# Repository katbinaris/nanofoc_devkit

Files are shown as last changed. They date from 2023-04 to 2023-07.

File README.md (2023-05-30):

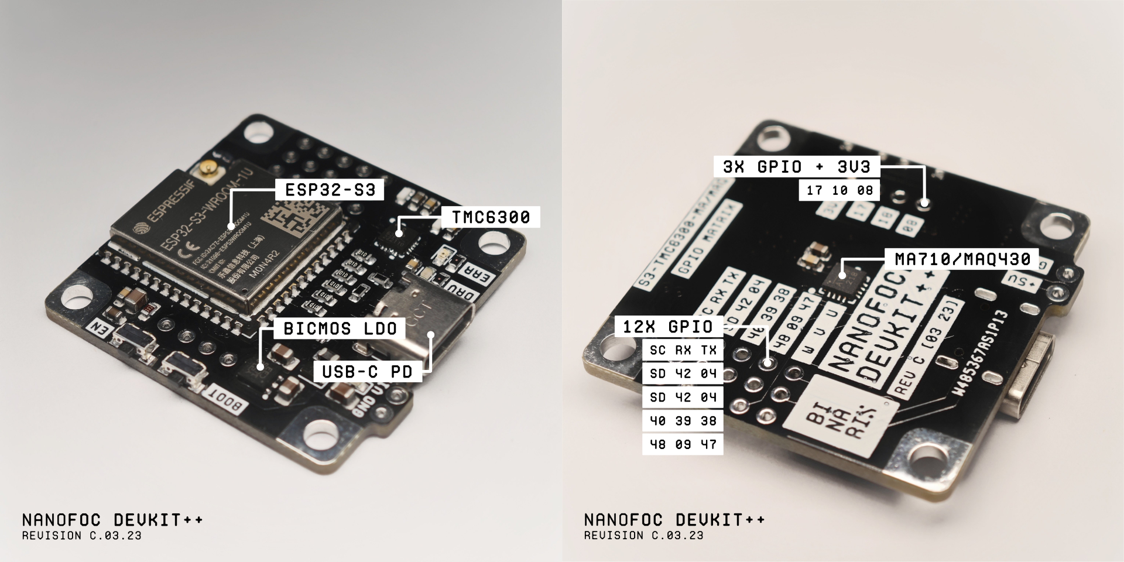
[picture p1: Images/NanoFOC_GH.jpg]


#### Product Description:
Starting your first Field Oriented Control (FOC) project might be daunting, especially if you're new to the field.

As makers, we frequently want to jump right into the action and begin writing the firmware without the hassle/need of selecting the right Microcontroller, Magnetic Sensor, and Motor Driver, then configuring and calibrating it with an abundance of cables that renders your projects too bulky to use in your creations.

The NanoFOC is little enough to attach on the back of most small BLDC gimbal motors (Even easier with Universal BLDC Motor Adapter Kit), making it an excellent choice for compact projects requiring maximum efficiency and precision.

Purchase Link: https://store.binaris.io/products/nanofoc-devkit

### Features:
- Espressif ESP32 S3 Microcontroller 4MB Flash, 2MB PSRAM 
- Trinamic TMC6300 low power 6PWM BLDC Driver
- MPS MagAlpha MA710 or MAQ430 rotary magnetic position sensor
- BiCMOS 3.3V LDO
- 11 Programmable GPIO's (SPI, PWM, ADC, RTC etc.)
- I2C & UART pins available
- USB Powered (Compatible with USB PD 2.0 - 5V @ 3A)
- USB OTG
- AUX Power via VIN pads 

### Pinout Cheat Sheet:
|  Pin | Function  | On GPIO Matrix? |
| --- | --- | --- |
| GPIO 01 | I2C SCL | YES |
| GPIO 02 |  I2C SDA | YES |
| GPIO 04 |  SPI CS -MAGNETIC SESNOR | NO |
| GPIO 05 |  SPI MOSI -MAGNETIC SESNOR | NO |
| GPIO 06 |  SPI SCLK -MAGNETIC SESNOR | NO |
| GPIO 07 |  SPI MISO -MAGNETIC SESNOR | NO |
| GPIO 08 |  I/O  | YES |
| GPIO 09 |  I/O  | YES |
| GPIO 10 |  VL - PhaseB Low  | NO |
| GPIO 11 |  WL - PhaseC Low  | NO |
| GPIO 12 |  UL - PhaseA Low  | NO |
| GPIO 13 |  WH - PhaseC High  | NO |
| GPIO 14 |  VH - PhaseB High  | NO |
| GPIO 17 |  I/O  | YES |
| GPIO 18 |  I/O  | YES |
| GPIO 19 |  USB D- | NO |
| GPIO 20 |  USB D+ | NO |
| GPIO 21 |  UH PhaseA High | NO |
| GPIO 38 |  I/O  | YES |
| GPIO 39 |  I/O  | YES |
| GPIO 40 |  I/O  | YES |
| GPIO 41 |  I/O  | YES |
| GPIO 42 |  I/O  | YES |
| GPIO 43 | UART0 TX or I/O  | YES |
| GPIO 44 | UART0 RX or I/O | YES |
| GPIO 43 | UART0 TX  | YES |
| GPIO 44 | UART0 RX | YES |
| GPIO 47 | I/O | YES |
| GPIO 48 | I/O | YES |

### Board Layout:

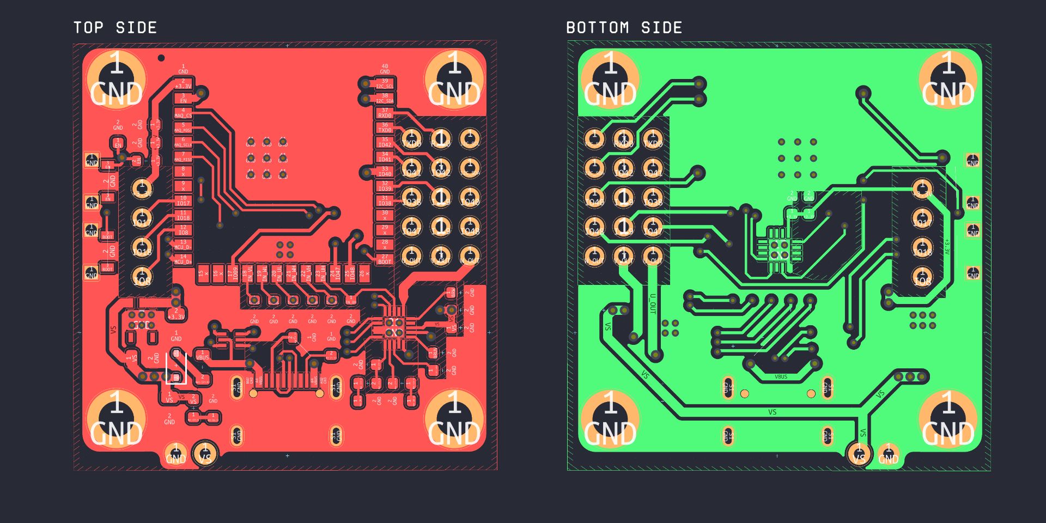
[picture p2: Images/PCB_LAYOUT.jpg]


### Bill Of Materials

| Component | References | Footprint | Quantity | Link | Price |
| --- | --- | --- | --- | --- | --- |
| 100nF | C1, C2, C4, C8, C12 | 0603 | 5 | https://eu.mouser.com/ProductDetail/KEMET/C0603C104K8RAC | 0,55 € |
| 4.7uF | C5, C6 | 0805 | 2 | https://eu.mouser.com/ProductDetail/TDK/C2012X7R1A475K125AC | 0,46 € |
| 10uF | C7, C13 | 0603 | 2 | https://eu.mouser.com/ProductDetail/Samsung-Electro-Mechanics/CL10A106KP8NNWC | 0,24 € |
| 22uf | C9 | 0805 | 1 | https://eu.mouser.com/ProductDetail/Murata-Electronics/GRM21BC81C226ME44L | 0,39 € |
| 22uf | C11 | 0603 | 1 | https://eu.mouser.com/ProductDetail/Murata-Electronics/GRM188R61A226ME15J | 0,17 € |
| 100K | R1-R6 | 0603 | 6 | https://eu.mouser.com/ProductDetail/Bourns/CMP0603-FX-1003ELF | 1,20 € |
| 300R | R7, R8 | 0603 | 2 | https://eu.mouser.com/ProductDetail/Panasonic/ERJ-UP3F3000V | 0,48 € |
| 150m | R9, R10 | 0603 | 2 | https://eu.mouser.com/ProductDetail/Susumu/KRL0816D-C-R150-F-T5 | 1,20 € |
| 340R | R14 | 0603 | 1 | https://eu.mouser.com/ProductDetail/Panasonic/ERJ-3EKF3400V | 0,09 €|
| 5.1K | R13 | 0603 | 2 | https://eu.mouser.com/ProductDetail/Panasonic/ERJ-P03F5101V | 0,70 € |
| 10K | R15 | 0603 | 1 | https://eu.mouser.com/ProductDetail/ROHM-Semiconductor/SFR03EZPF1002 | 0,13 € |
| 100Mhz 400Ohm 1.5A | L1 | 0805 |  1 | https://eu.mouser.com/ProductDetail/Laird-Performance-Materials/MI0805K400R-10 | 0,19 €  |
| NUF2042XV6T1G | D3 | SOT-563 | 1 | https://www.mouser.com/ProductDetail/onsemi/NUF2042XV6T1G | 0,44 € |
| CUS15S30 | D4 | SOD-323 | 1 | https://www.mouser.com/ProductDetail/Toshiba/CUS15S30H3F | 0,33 € |
| Yellow/Green Mono LED | D5, DRV | 0603 | 2 | https://eu.mouser.com/ProductDetail/ROHM-Semiconductor/SML-D12M8WT86 | 0,68 € |
| ESP32-S3 N4R2 1U | U1 | ESP32-S3-WROOM-1U | 1 | https://www.mouser.com/ProductDetail/Espressif-Systems/ESP32-S3-WROOM-1U-N8R2 | 3,38 € |
| TMC6300 LA | U2 | QFN20 | 1 | https://eu.mouser.com/ProductDetail/ADI-Trinamic/TMC6300-LA-T | 2,13 € |
| MPS MA710| U3 | QFN16 | 1 | https://www.mouser.com/ProductDetail/Monolithic-Power-Systems-MPS/MA710GQ-Z | 6,15 € |
| Alps SKTDLDE010 | SW1, SW2 | SKTDLDE010 | 2 | https://eu.mouser.com/ProductDetail/Alps-Alpine/SKTDLDE010 | 1,46 € |
| Amber Mono LED | ERR | 0603 | 1 | https://eu.mouser.com/ProductDetail/Wurth-Elektronik/150060AS75000 | 0,14 € |
| ST1L05CPU33R LDO | IC1 | DFN6 | 1 | https://www.mouser.com/ProductDetail/STMicroelectronics/ST1L05CPU33R | 1,18 € |
| G-Switch_GT-USB-7010ASV | P1 | 7010ASV | 1 | https://www.mouser.com/ProductDetail/GCT/USB4105-GF-A | 0,75 € | 
| | | | **38** | | **22,44 € / 23.50 $** |

### Power Options:
Device is designed to run of 5V @ 1.5A Max.
There are two ways you can power the board 

1. USB Type C - Power delivery is capped at 5V3A with usage of 5.1K resistors on CC1 and CC2 pads. It is recommended to use USB that is PD2.0 compatible.
It is possible to power device off 500mA capable USB port - however this is not recommended.

2. External VIN  - This connection bypass L1 and  D4 connecting directly to Driver and LDO VS pin. The recommended input voltage is 5V and maximum allowed is 6V - which is restricted by max VIN of ST1L05C LDO.

### First Time Setup
Development Kit comes with no Firmware.
Since ESP32-S3 comes with USB-OTG/USB-Serial integrated into MCU the assumption is that this would be a preferred method of code upload.
If you are connecting your device to computer for the first time it is critical to put device into DFU mode.

**In order to do that you need to:**
1. Connect Development Board to USB port - *On windows machines you may notice that USB detection sound goes on and off in loop - Please ignore that for now*
2. Press and hold **BOOT** switch
3. While holding **BOOT** press and hold **RESET** switch for about **2 seconds**
4. Release **RESET**
5. Release **BOOT**
6. You are now in **DFU mode** and you can use Arduino IDE or PlatformIO to upload your first sketch.

Alternatively you may use UART pins which are available on GPIO Matrix to upload your code the legacy way.
In order to do that you need external TTL Converter.

### Projects using NanoFOC:

SmartKnob by Scott Bezek -> https://github.com/scottbez1/smartknob#nanofoc-3rd-party

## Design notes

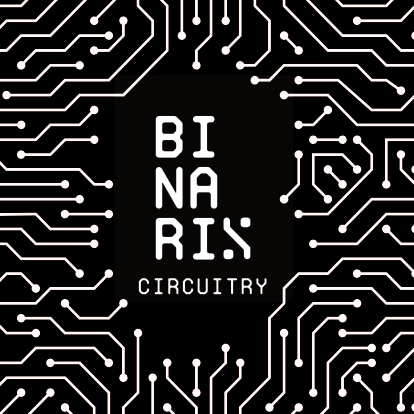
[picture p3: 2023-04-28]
Images/Sticker_large.png

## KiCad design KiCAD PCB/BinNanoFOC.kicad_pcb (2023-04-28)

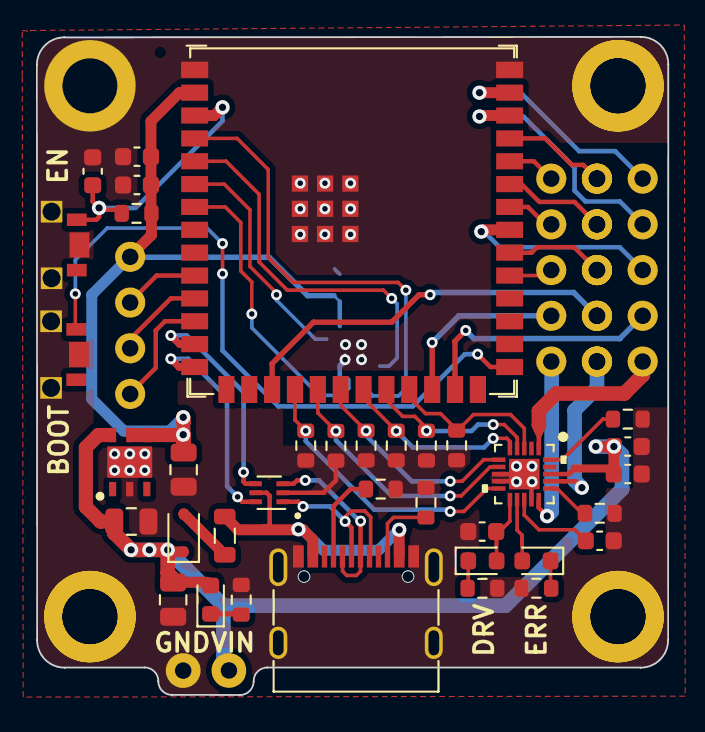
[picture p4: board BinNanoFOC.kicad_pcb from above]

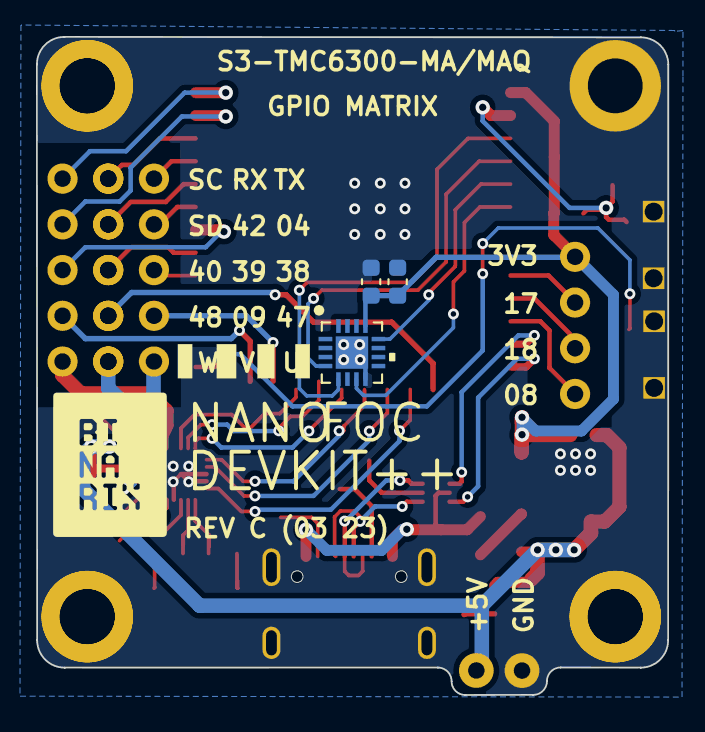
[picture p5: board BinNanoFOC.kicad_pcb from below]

Board: 2 copper layers, 35.1 x 36.6 mm, 39 parts (3 on the bottom side), 30 nets.

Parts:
C1, C2, C4, C8, C12: 100nF; C_0603_1608Metric
C3: 10uF; C_0603_1608Metric
C5, C6: 4.7uF; C_0805_2012Metric
C7, C13: 1uF; C_0603_1608Metric
C9: 22uF; C_0805_2012Metric
C11: 22uF; C_0603_1608Metric
D3: NUF2042XV6T1G; SOT-563
D4: D; D_SOD-323
D5: LED; LED_0603_1608Metric
DIAG: ERROR; LED_0603_1608Metric
DRV: DRIVER; LED_0603_1608Metric
IC1: ST1L05CPU33R; SON95P300X300X100-7N-D
L1: 100Mhz 40Ohm 1.5A; L_0805_2012Metric
P1: USB_C_Plug; USB_C_Receptacle_G-Switch_GT-USB-7010ASV
R1, R2, R3, R4, R5, R6: 100K; R_0603_1608Metric
R7, R8: 300R; R_0603_1608Metric
R9, R10: 300M; R_0603_1608Metric
R13, R13#2: 5.1K; R_0603_1608Metric
R14: 350R; R_0603_1608Metric
R15: 10K; R_0603_1608Metric
SW1, SW2: SW_MEC_5E; SKTDLDE010
U1: ESP32-S3-WROOM-1; ESP32-S3-WROOM-1U
U2: TMC6300-LA
U3: MAQ430GQE-AEC1-P

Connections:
+3.3V: C6.2, C7.1, C8.1, C11.1, C12.1, IC1.4 (VO), IC1.5 (V_O_SENSE), R15.1, U1.2 (3V3), U3.13 (VDD)
BOOT: SW1.3 (K), U1.27 (GPIO0/BOOT)
BRUV: R9.1, U2.16 (BRUV)
BRW: R10.1, U2.20 (BRW)
EN: C13.1, R15.2, SW2.3 (K), U1.3 (EN)
GND: C1.2, C2.2, C3.2, C4.2, C5.2, C6.1, C7.2, C8.2, C9.2, C11.2, C12.2, C13.2, D3.2 (GND), IC1.2 (GND), IC1.7 (EP), P1.A1 (GND), P1.A12 (GND), P1.B1 (GND), P1.B12 (GND), P1.S1 (SHIELD), R1.2, R2.2, R3.2, R4.2, R5.2, R6.2, R7.2, R8.2, R9.2, R10.2, R13.1, R13#2.1, R14.2, SW1.1, SW1.2, SW2.1, SW2.2, U1.1 (GND), U1.40 (GND), U1.41 (GND), U2.8 (GND), U2.9 (GND), U2.14 (GND), U2.21 (EPAD), U3.8 (GND), U3.17 (PAD)
IN_UH: R6.1, U1.23 (GPIO21), U2.3 (UH)
IN_UL: R3.1, U1.20 (GPIO12/TOUCH12/ADC2_CH1/FSPICLK/FSPIIO6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), U2.6 (UL)
IN_VH: R5.1, U1.22 (GPIO14/TOUCH14/ADC2_CH3/FSPIWP/FSPIDQS/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), U2.4 (VH)
IN_VL: R1.1, U1.18 (GPIO10/TOUCH10/ADC1_CH9/FSPICS0/FSPIIO4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), U2.10 (VL)
IN_WH: R4.1, U1.21 (GPIO13/TOUCH13/ADC2_CH2/FSPIQ/FSPIIO7/S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), U2.5 (WH)
IN_WL: R2.1, U1.19 (GPIO11/TOUCH11/ADC2_CH0/FSPID/FSPIIO5/S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), U2.7 (WL)
MAQ_CS: U1.4 (GPIO4/TOUCH4/ADC1_CH3), U3.5 (CS)
MAQ_MISO: U1.7 (GPIO7/TOUCH7/ADC1_CH6), U3.7 (MISO)
MAQ_MOSI: U1.5 (GPIO5/TOUCH5/ADC1_CH4), U3.4 (MOSI)
MAQ_SCLK: U1.6 (GPIO6/TOUCH6/ADC1_CH5), U3.12 (SCLK)
MCU_D+: D3.6 (D1(0)), U1.14 (GPIO20/U1CTS/ADC2_CH9/CLK_OUT1/USB_D+)
MCU_D-: D3.4 (D2(0)), U1.13 (GPIO19/U1RTS/ADC2_CH8/CLK_OUT2/USB_D-)
unnamed: C1.1, DRV.2 (A), U2.11 (VIO/NSTDBY)
unnamed: DRV.1 (K), R7.1
unnamed: DIAG.2 (A), U2.12 (DIAG)
unnamed: DIAG.1 (K), R8.1
unnamed: D4.2 (A), L1.2
unnamed: D5.1 (K), R14.1
unnamed: P1.A5 (CC), P1.B5 (VCONN), R13.2, R13#2.2
unnamed: C2.1, U2.13 (1-8VOUT)
USB_D+: D3.1 (D1(I)), P1.A6 (D+), P1.B6
USB_D-: D3.3 (D2(I)), P1.A7 (D-), P1.B7
VBUS: D3.5 (VBUS), L1.1, P1.A4 (VBUS), P1.A9 (VBUS), P1.B4 (VBUS), P1.B9 (VBUS)
VS: C3.1, C4.1, C5.1, C9.1, D4.1 (K), D5.2 (A), IC1.6 (VI), U2.18 (VS)

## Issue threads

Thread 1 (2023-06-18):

BOM mistake

giklette, 2023-06-18:
on the README.md
goto the BOM components : https://github.com/katbinaris/nanofoc_devkit#bill-of-materials

should replace the row C7, C13 by C7, C3
and add new row
> 1uf      |    C13     |     0603    |      1     |     // mouser reference //

- C3 is 10uF
- C13 is 1uF    not   10uF

Jogius, 2024-03-22:
C7 is also 1uF, according to the PCB file. So C7 and C13 should be 1uF instead of 10uF, and C3 needs to be added to the file altogether.

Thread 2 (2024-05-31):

Schematic for LDO incorrect / wrong part number (ST1L05CPU33R)

Jogius, 2024-05-31:
I tried assembling my first nanofoc yesterday and I think I might've found a small mistake in the schematic or in the part listed.

The LDO is an ST1L05CPU33R, which is listed under ST1L05C in the datasheets. This version of the LDO has an enable Pin, which is not connected on the PCB. I was able to make a small bridge to the capacitor right next to it, which successfully enabled the 3.3V output.
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

I believe the part should either be an ST1L05 (without the C) or there needs to be another connection to this chip.

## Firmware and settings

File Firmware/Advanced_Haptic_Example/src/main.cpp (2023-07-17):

#include <Arduino.h> // PIO Specific Call Arduino Core
#include <SimpleFOC.h> // Call FOC Library
#include <utils.h> // ESP32 Specific utility that clamps a middle value witin a range of values between a defined min and max bound.

// Driver Logic Pin Defs
#define PIN_UH 21
#define PIN_UL 12
#define PIN_VH 14
#define PIN_VL 10
#define PIN_WH 13
#define PIN_WL 11
// Sensor nCS pin
#define MAQ_SS 4
//Motor Pole Pair Count
#define MOTOR_PP 7 

// Static construct set for Dead Zone Compensation and EWMA correction.
static const float DEAD_ZONE_DETENT_PERCENT = 0.2;
static const float DEAD_ZONE_RAD = 1 * _PI / 180;
static const float IDLE_VELOCITY_EWMA_ALPHA = 0.001;
static const float IDLE_VELOCITY_RAD_PER_SEC = 0.05;
static const uint32_t IDLE_CORRECTION_DELAY_MILLIS = 500;
static const float IDLE_CORRECTION_MAX_ANGLE_RAD = 5 * PI / 180;
static const float IDLE_CORRECTION_RATE_ALPHA = 0.0005;

// Default Haptic Program Variables
int32_t position = 0;
int32_t num_positions = 360;
float position_with_radians = 2.5*_PI/180.0;;
float haptic_strength_unit = 0.2;
float haptic_endstop_strength_unit = 1.4;
float haptic_dampening_factor = 5500; // min 50 max 7500
float snap_point = 0.545;
float sub_position_unit;

 
  float idle_check_velocity_ewma = 0;
  uint32_t last_idle_start = 0;
  uint32_t last_publish = 0;

  const float derivative_lower_strength = haptic_strength_unit * 0.148;
  const float derivative_upper_strength = haptic_strength_unit * 0.008;
  const float derivative_position_width_lower = radians(3); // 3 Degrees represented in radians
  const float derivative_position_width_upper = radians(8); // 8 Dergees represented in radians
  const float raw = derivative_lower_strength + (derivative_upper_strength - derivative_lower_strength)/(derivative_position_width_upper - derivative_position_width_lower)*(position_with_radians - derivative_position_width_lower);



// This code is optimized to works well with MAD2804 motor.

// Call a MagneticSensoSPI driver in SimpleFOC libdep.
// You will need to manually add definiton of the sensor to MagneticSensorSPI.h and MagneticSensorSPI.cpp
// .pio/libdeps/adafruit_feather_esp32s3/SimpleFOC/src/drivers/sensors
// Correct version of the file for SimpleFOC 2.3 can be found in GitHub repository
MagneticSensorSPI sensor = MagneticSensorSPI(MAQ430_SPI, MAQ_SS); 

// Define number of Stator Pole Pairs - Usually this number resides between 7-11 for most gimbal motors
// If you're unsure how many pole pairs your motor has, SimpleFOC calibration would help you estimating PP Count
// Alternatively SimpleFOC has example code "Pole Pair Estimator"
BLDCMotor motor = BLDCMotor(MOTOR_PP);
// BLDCDriver6PWM(PIN_UH, PIN_UL, PIN_VH, PIN_VL, PIN_WH, PIN_WL);
BLDCDriver6PWM driver = BLDCDriver6PWM(PIN_UH, PIN_UL, PIN_VH, PIN_VL, PIN_WH, PIN_WL);

void setup() {

  // SimpleFOC Setup

  // initialise magnetic sensor hardware
  sensor.init();

  // link the motor to the sensor
  motor.linkSensor(&sensor);

  // Driver Configuration
  // power supply voltage [V]
  driver.voltage_power_supply = 5;

  // Driver Voltage limit - A way to limit PWM duty cycle
  // For NanoFOC DevKit this value is between 2-5V
  // Do not exceed 5V as you might damage the driver
  driver.voltage_limit = 3;

  // Driver PWM Frequency - Higher the value the smoother operation in theory.
  // If unsure leave commented, Values can range from 8000-50000 (Hz)
  // driver.pwm_frequency = 50000;

  // Initialize Driver
  driver.init();
  // Link the motor and the driver
  motor.linkDriver(&driver);

  // For Haptic Feedback we will be using Torque controller
  // Torque Controller can be controlled by Voltage (Default), Voltage - Estimated Current, DC Current and FOC Current modes.
  
  motor.controller = MotionControlType::torque;

  // If you know your motor phase resistance
  // You can uncomment this section, and you will be operating in "Voltage - Estimated Current" mode.
  // It is much more natural to control haptics with Current rather than Voltage
  // motor.phase_resistance = 4.4; // ex. 2.5 Ohms

  // If you know your motor KV rating (V/RPM) you may instert it here. KV is proportional to target voltage.
  // Most of manufacturers provide KV rating for rated Voltage, It is advised to perform your own KV rating.
  // You can do this by running SimpleFOC KV Rating example code.
  // Please add 10-20% overhead on top of your KV estimation
  //motor.KV_rating = 115;

  // IMPORTANT
  // By introducing Phase Resistance and KV Rating you would need drastically lower your PID values
  // If you decide to introuce Phase R and KV rating start from PID 0,0,0,250,5
  // High probability that BEMF/Inductance spike will damage VBUS diode and LDO if not used correctly


  // Very Basic PID Controller
  // haptic attraction controller - only Proportional + Derivative (Ignore Intergal == 0)
  // P = Proportional, responsible for reactiveness, Values between 0.1 - 1.5 are acceptable for most of motors.
  // D = Derivative, responsible for introducing resistance - similar to viscose friction. Use this to counteract cogging torque or in combination with Proportional. (Keep values low between 0.01 = 0.14)
  // Output_Ramp = Output Derivative limit [V/s] - depending on motor keep it between 100-2500. Non NdFeB drives can use higher values.
  // Limit = Output supply limit [V] - Keep at 3 or less unless you understand what you're doing.
  // [IMPORTANT] If you're not using MAD2804 motor start tuning from PID{0,0,0,100,1}
  // Set motor voltage limit (it is safe to keep it between 2.5-5V, depending on motor is recommended 3V)
  motor.voltage_limit = 3;   // [V]
  motor.PID_velocity.P = 1; // Proportional Gain is further calculated adaptively
  motor.PID_velocity.I = 0; // Intergal Gain remain at "0"
  motor.PID_velocity.D = 0.48; // Derivative Gain is further calculated adaptively as well
  motor.PID_velocity.output_ramp = haptic_dampening_factor; // TODO Output Ramp need to be adaptive 
  motor.PID_velocity.limit = 3; // Velocity limit is further calculated adaptively

  // Velocity Low Pass Filtering
  // Default value is 5ms - You an try different values to see what is best for your motor
  // The lower value the less filtering
  // motor.LPF_velocity.Tf = 0.015;// to set it to 10ms
  // As above but for angle (does not override velocity Low Pass Filtering)
  motor.LPF_angle.Tf = 0.0075;
  
  motor.PID_velocity.D = CLAMP(
    raw,
    min(derivative_lower_strength, derivative_upper_strength),
    max(derivative_lower_strength, derivative_upper_strength)
  );

  // Use monitoring with serial 
  Serial.begin(115200);

  // Comment out if not needed
  motor.useMonitoring(Serial);

  // Initialize motor
  motor.init();
  

  // Align sensor, PP check + Eletrical Zero, if pass start FOC
  motor.initFOC(4.6, Direction::CW);

  Serial.println("Haptic Device Ready :)");
  _delay(500);

  

}

float current_angle_center = -motor.shaft_angle;

void loop() {
 
  // Main FOC algorithm function
  motor.loopFOC();

 // If we are not moving and we're close to the center (but not exactly there), slowly adjust the centerpoint to match the current position
  idle_check_velocity_ewma = motor.shaft_velocity * IDLE_VELOCITY_EWMA_ALPHA + idle_check_velocity_ewma * (1 - IDLE_VELOCITY_EWMA_ALPHA);
  if (fabsf(idle_check_velocity_ewma) > IDLE_VELOCITY_RAD_PER_SEC) {
      last_idle_start = 0;
  } else {
      if (last_idle_start == 0) {
          last_idle_start = millis();
      }
  }
  if (last_idle_start > 0 && millis() - last_idle_start > IDLE_CORRECTION_DELAY_MILLIS && fabsf(motor.shaft_angle - current_angle_center) < IDLE_CORRECTION_MAX_ANGLE_RAD) {
      current_angle_center = motor.shaft_angle * IDLE_CORRECTION_RATE_ALPHA + current_angle_center * (1 - IDLE_CORRECTION_RATE_ALPHA);
  }

float position_to_indent_center = -motor.shaft_angle - current_angle_center;

if (position_to_indent_center > position_with_radians * snap_point && (num_positions <= 0 || position > 0)) {
            current_angle_center += position_with_radians;
            position_to_indent_center -= position_with_radians;
            position--;
            
        } else if (position_to_indent_center < -position_with_radians * snap_point && (num_positions <= 0 || position < num_positions - 1)) {
            current_angle_center -= position_with_radians;
            position_to_indent_center += position_with_radians;
            position++;
           
        }

float dead_zone_adjustment = CLAMP(
  position_to_indent_center,
  fmaxf(-position_with_radians*DEAD_ZONE_DETENT_PERCENT, -DEAD_ZONE_RAD),
  fminf(position_with_radians*DEAD_ZONE_DETENT_PERCENT, DEAD_ZONE_RAD));

bool out_of_range = num_positions > 0 && ((position_to_indent_center > 0 && position == 0) || (position_to_indent_center < 0 && position == num_positions - 1));
motor.PID_velocity.limit = 20;
motor.PID_velocity.P = out_of_range ? haptic_endstop_strength_unit : 3.4;

// Apply motor torque based on our angle to the nearest detent (detent strength, etc is handled by the PID_velocity parameters)
if (fabsf(motor.shaft_velocity) > 50) {
    // Don't apply torque if velocity is too high (helps avoid positive feedback loop/runaway)
    motor.move(0);
} else {
    float torque = motor.PID_velocity(-position_to_indent_center + dead_zone_adjustment);
    torque = -torque;
    motor.move(torque);
}

// Publish current status to other registered tasks periodically
        if (millis() - last_publish > 10) {
            Serial.print("Current Position: ");
            Serial.print(position + 1);
            Serial.print(" (Derivative: ");
            Serial.print(motor.PID_velocity.D);
            Serial.print(" Proportional: ");
            Serial.print(motor.PID_velocity.P);
            Serial.println(").");
            last_publish = millis();
        }
  
  // Real-time monitoring calls
  // motor.monitor();
  // real-time commander calls
  // command.run();

  // Add microdelay for "Clickiness"
  // Use value between 100-400us. Especially for higher PID or Attractor angle use low values!
  // Do not exceed 1000us
  delayMicroseconds(275);
}

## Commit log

2023-04-28 Init
    Updated Rev.C.3.23, PCB, Schematic & Project.
    [BinNanoFOC.kicad_pcb, BinNanoFOC.kicad_sch]
2023-04-28 KiCad Update
    [BinNanoFOC.kicad_pcb, BinNanoFOC.kicad_sch, BinNanoFOC_BLDC_BaseAdapter_1_6mm.kicad_pcb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]
2023-05-15 Update safe PID values
2023-05-30 Updated BOM + Link to SmartKnob
